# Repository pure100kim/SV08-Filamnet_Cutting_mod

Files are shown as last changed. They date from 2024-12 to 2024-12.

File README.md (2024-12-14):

# SV08 Filament Cutting MOD

Bamboo Hotend integrated filament cutting mode.

I have modified the STEP CAD file available on Sovol's GitHub.
Thank you to Sovol for providing the CAD STEP files.

https://github.com/Sovol3d/SV08/tree/main/STEP

<br>
<br>
<br>

**아래 동작 유투브 영상 참조하세요~** 
(Please refer to the YouTube video for the following steps~)

Refer to operation youtube video as below.

https://www.youtube.com/watch?v=FpVqoYQupSA

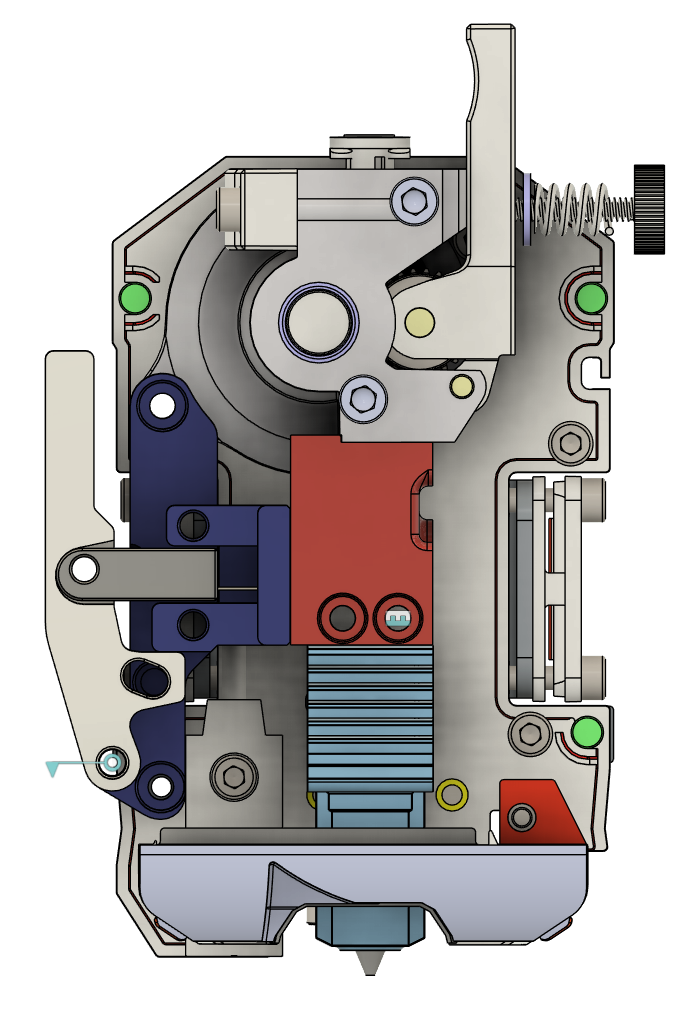
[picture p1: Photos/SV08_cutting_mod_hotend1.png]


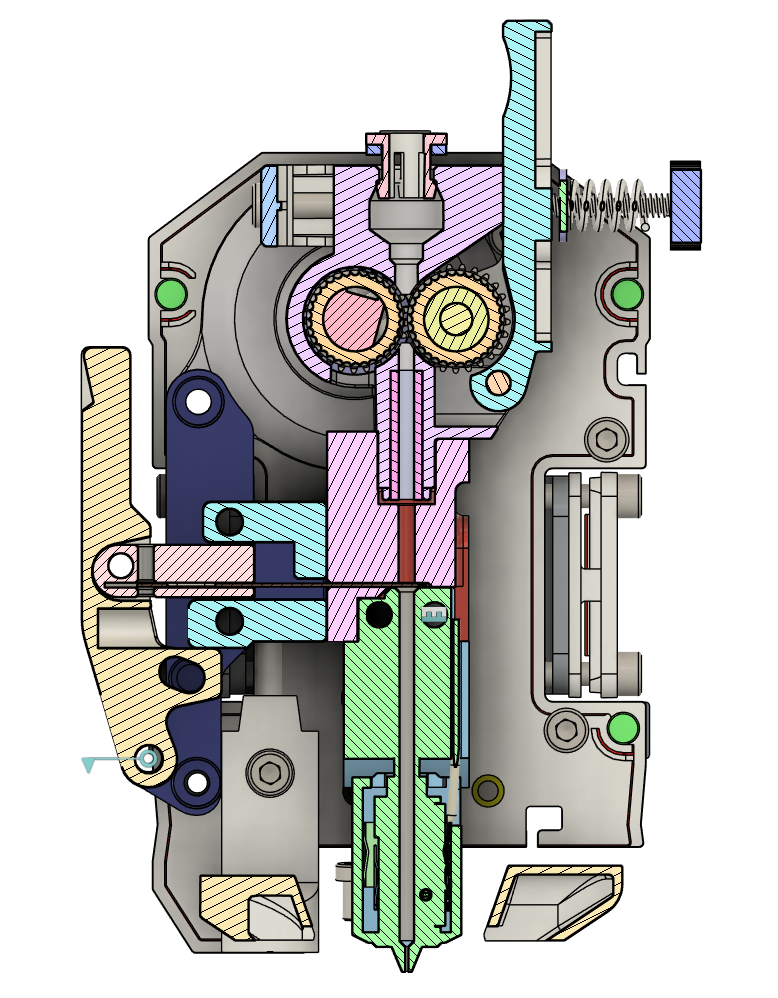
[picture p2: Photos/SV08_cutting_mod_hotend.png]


## **1. Prepare parts**

(1) Bambu HOTEND : 1ea

(2) Blade Cutter : 1ea

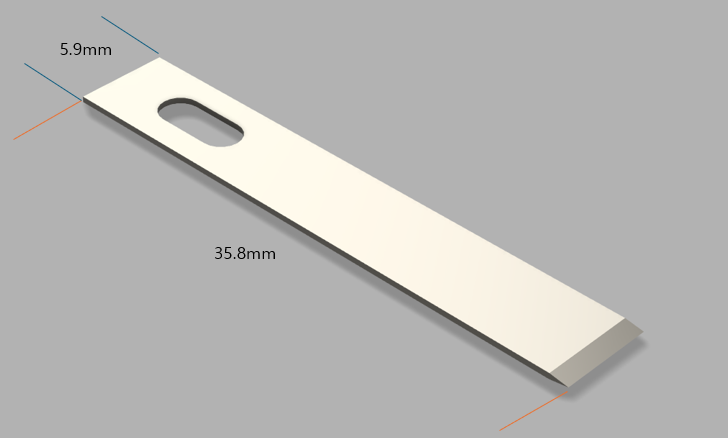
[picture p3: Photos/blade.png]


(3) M3 Insert : 5ea

(4) pen spring : 1ea

(5) space : 2ea

(6) M2*4mm : 1ea  (blade for fixing)

(7) M3*16mm : 3ea

(8) M3*20mm (SHCS) : 3ea

(9) M3*20mm (BHCS) : 2ea

(10) M3*8mm : 1ea

(11) M3 nut : 1ea (required loctite after joint)

(12) M4*20 : 1ea

<br>
<br>

## **2. Insert assembly**

인서트를 아래 사진과 같이 삽입을 합니다.<br>
The insert is inserted as shown in the image below.<br>

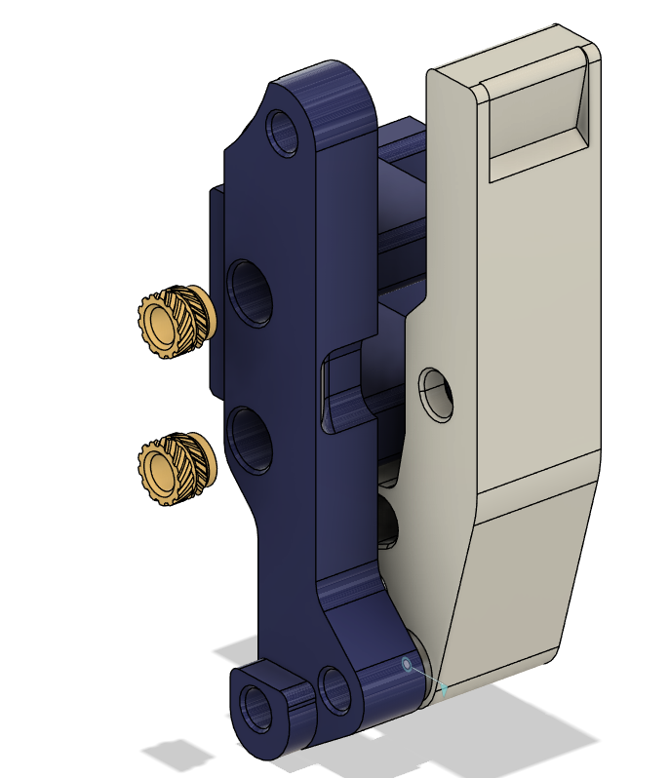
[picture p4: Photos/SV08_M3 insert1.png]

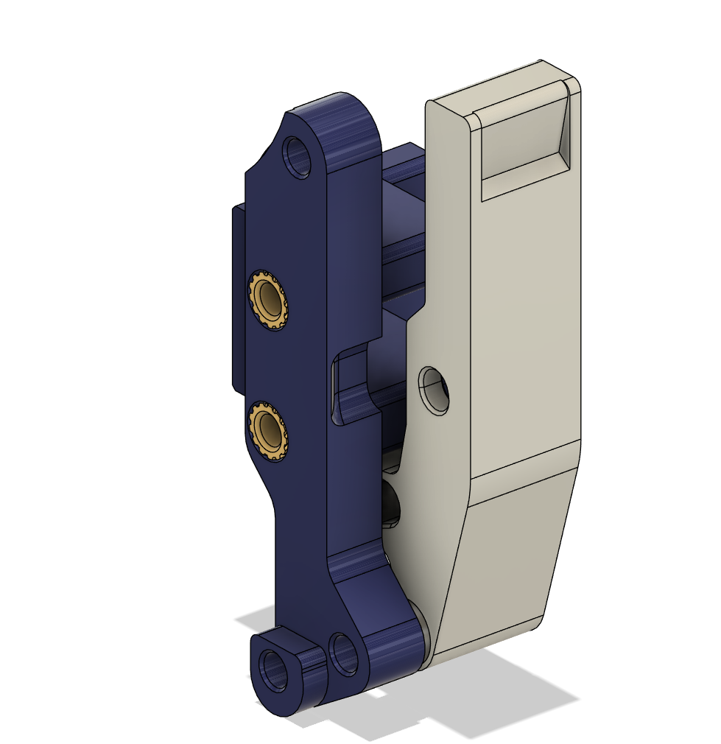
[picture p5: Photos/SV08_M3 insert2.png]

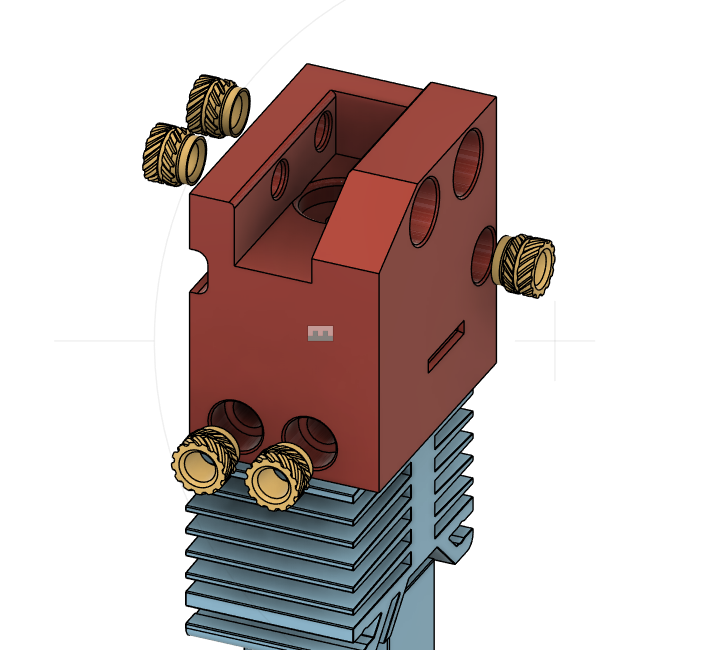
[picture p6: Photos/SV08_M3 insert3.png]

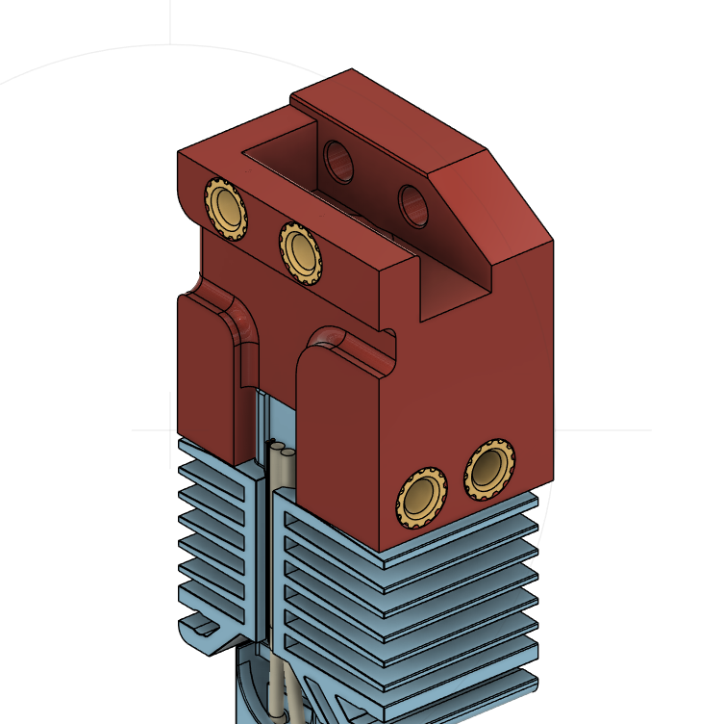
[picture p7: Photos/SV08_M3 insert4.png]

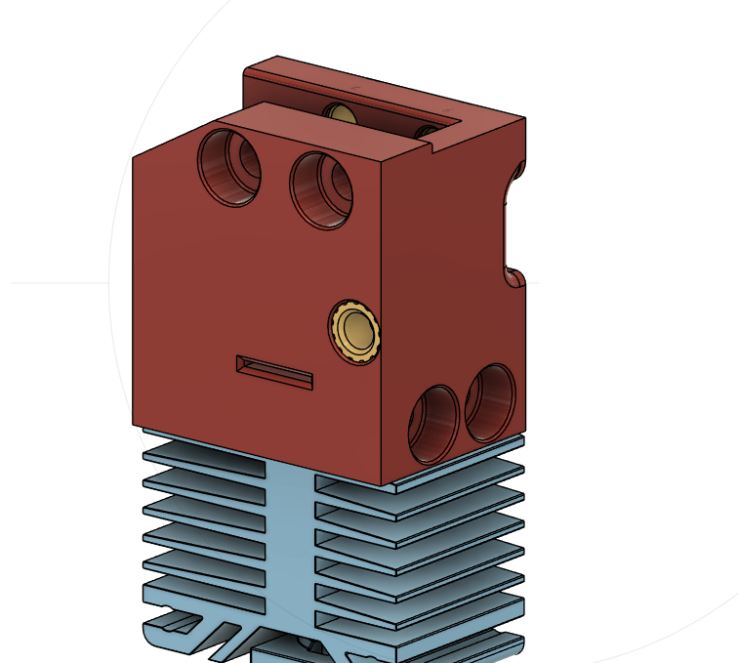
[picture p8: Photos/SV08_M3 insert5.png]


<br>

(1) HOTEND와 마운트를 먼저 체결합니다.<br>
First, attach the HOTEND and the mount. <br>
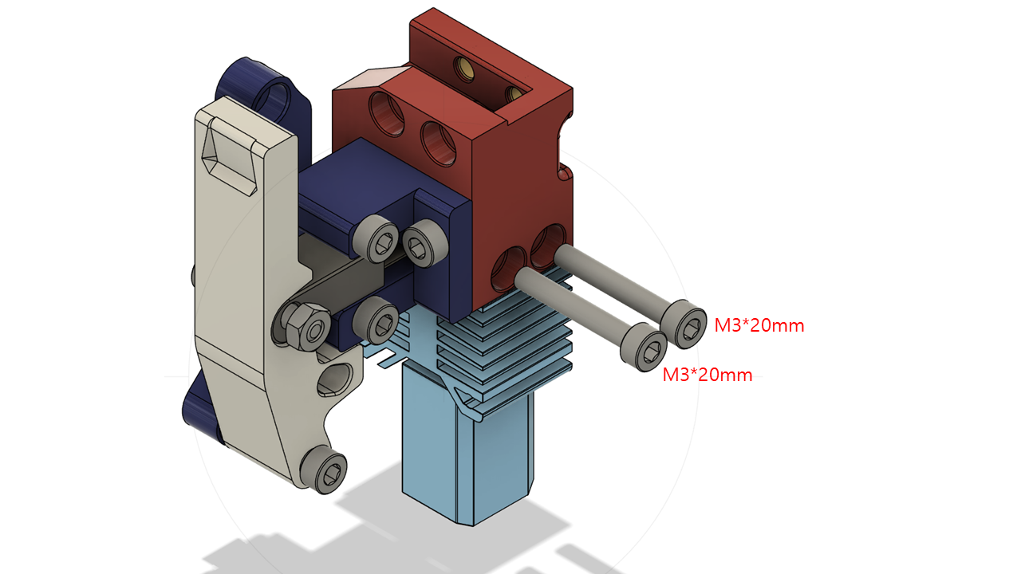
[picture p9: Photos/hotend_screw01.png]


<br>
<br>
(2) 마운트를 헤더에 체결을 합니다.<br>
Attach the mount to the header. <br>

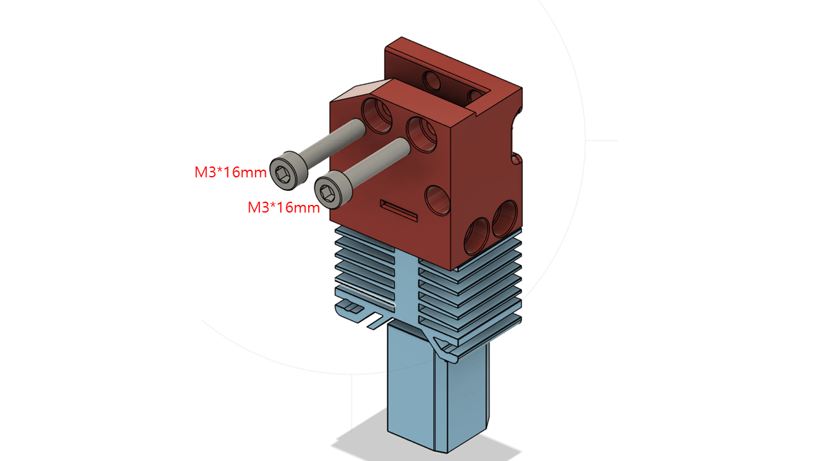
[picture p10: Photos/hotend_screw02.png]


<br>
<br>
(3) 레버 마운트를 헤더에 체결합니다.<br>
Attach the lever mount to the header. <br>

<br>
<br>
(4) 컷팅 가이드를 HOTEND 마운트와 체결합니다.<br>
Attach the cutting guide to the HOTEND mount. <br>

<br>
<br>
(5) 칼날과 칼날 마운트를 M2 볼트로 조립합니다.<br>
Assemble the blade and blade mount using M2 bolts. <br>

<br>
(6) 칼날 조립 부품을 헤더쪽에 가이드에 맞춰 삽입합니다.<br>
Insert the blade assembly component into the header, aligning it with the guide. <br>

<br>

(7) 칼날 가이드 레일을 레버 마운트와 M3*20mm 2개로 고정합니다.<br>
Secure the blade guide rail to the lever mount using two M3*20mm screws. <br>

(8) 레버 하단부 M3*20mm로 레버 마운트에 체결입니다.<br>
    M3 SPACE(와셔)를 양쪽에 넣어주면 좋습니다.<br>    
    (주의) 레버가 움직이도록 꽉 체결하지 말 것! 움직여야 합니다.<br>

Secure the lower part of the lever to the lever mount using an M3*20mm screw. <br>
It is recommended to insert M3 spacers (washers) on both sides. <br>
(Caution) Do not tighten the lever too firmly! It must remain movable. <br>

(9) 칼날 마운트 부품과 레버를 조립합니다. <br>
    M3 너트와 체결하며 록타이트로 너트가 빠지지 않도록 합니다.<br>
    (옵션) M3너트 안쪽에  M4 스페이스를 추가해도 됩니다.<br>    
    (주의) 칼날 마운트와 꽉 체결하지 말 것! 움직여야 합니다.<br>
Assemble the blade mount component with the lever. <br>
Secure them with an M3 nut, and apply Loctite to prevent the nut from loosening. <br>
(Optional) You may add an M4 spacer inside the M3 nut. <br>
(Caution) Do not tighten the blade mount too firmly! It must remain movable. <br>
    
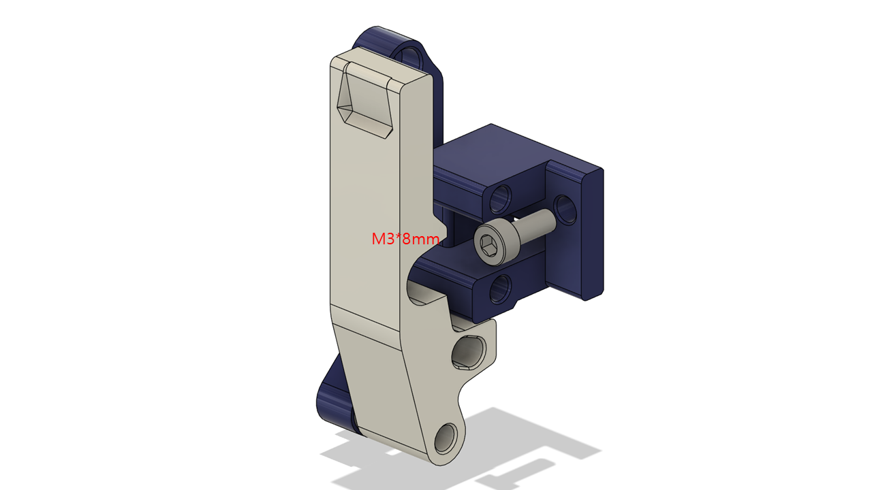
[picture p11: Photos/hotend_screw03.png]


(10) 레버를 움직이며 칼날이 자연스레 움직이는지 확인합니다. <br>
     (필수) 둥근머리 볼트(BHCS)를 사용해야 팬의 무두 볼트와 간섭이 생기질 않습니다.<br>
     (선택) 팬 고정 볼트를 둥근머리 볼트로 변경하여도 됩니다.<br>

 Move the lever to ensure the blade moves smoothly. <br>
(Mandatory) Use button head cap screws (BHCS) to avoid interference with the fan’s headless bolts. <br>
(Optional) You may also replace the fan mounting bolts with button head cap screws. <br>

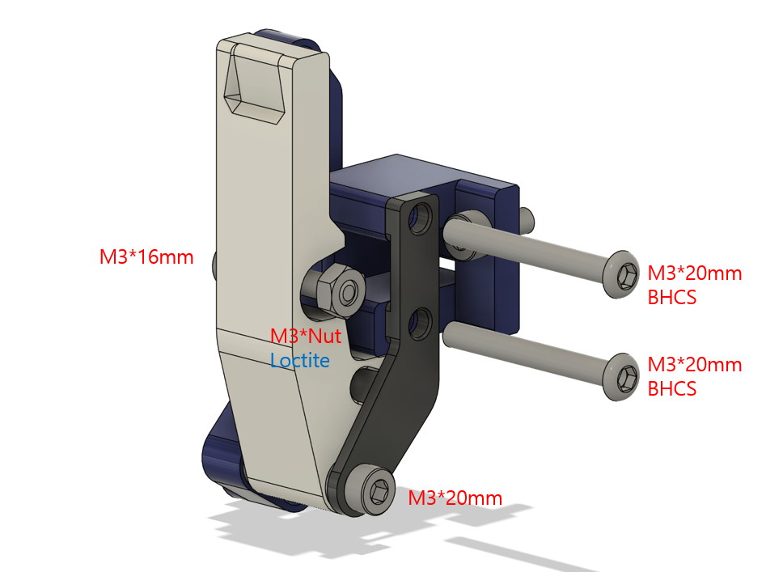
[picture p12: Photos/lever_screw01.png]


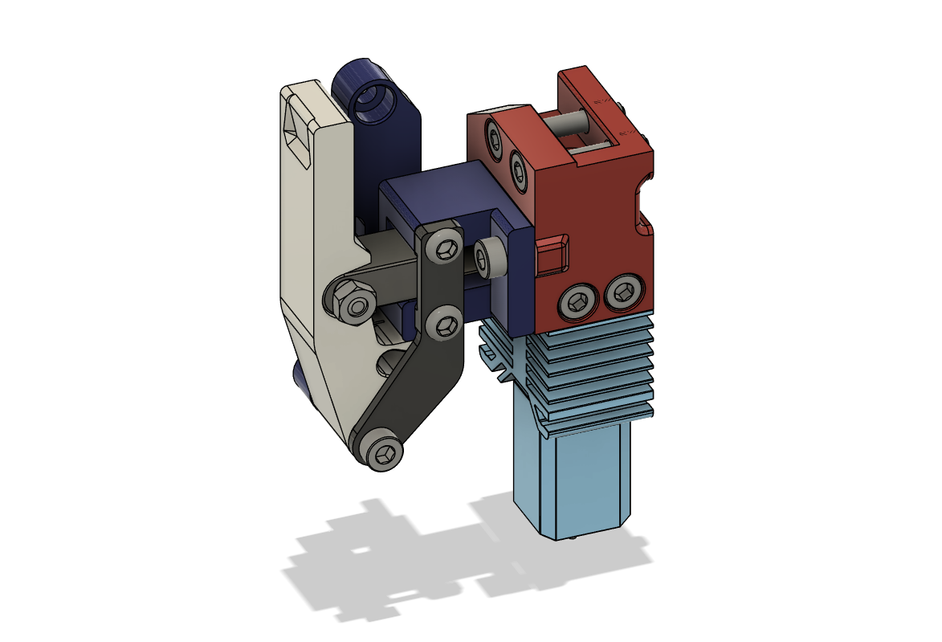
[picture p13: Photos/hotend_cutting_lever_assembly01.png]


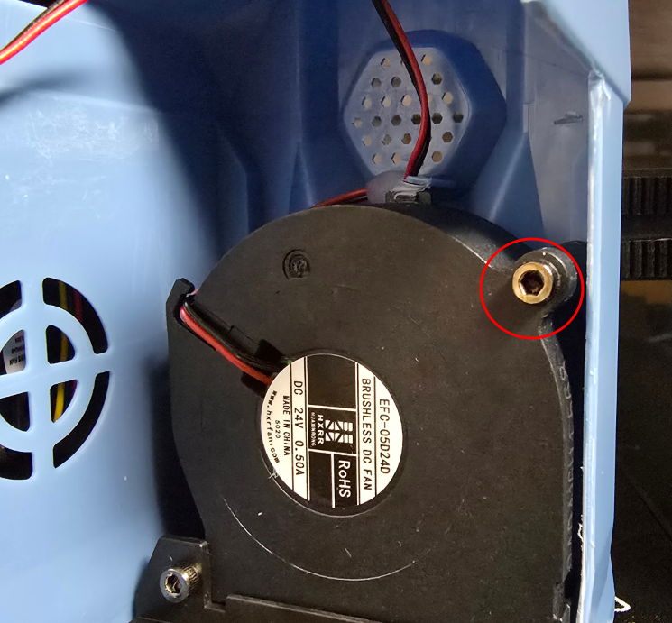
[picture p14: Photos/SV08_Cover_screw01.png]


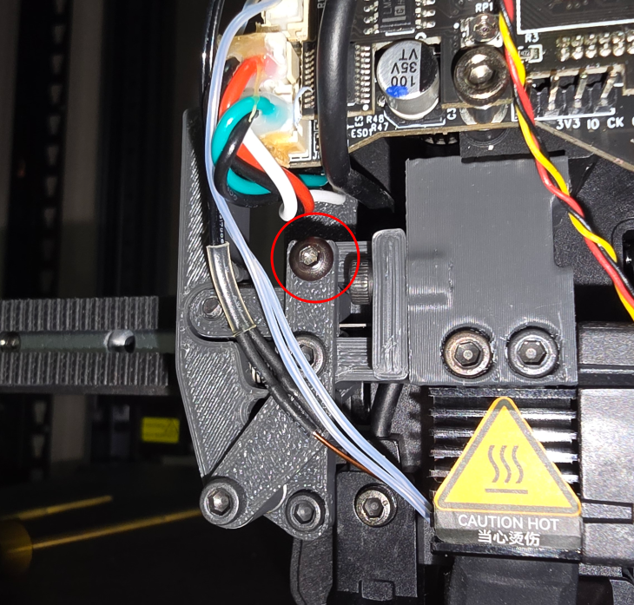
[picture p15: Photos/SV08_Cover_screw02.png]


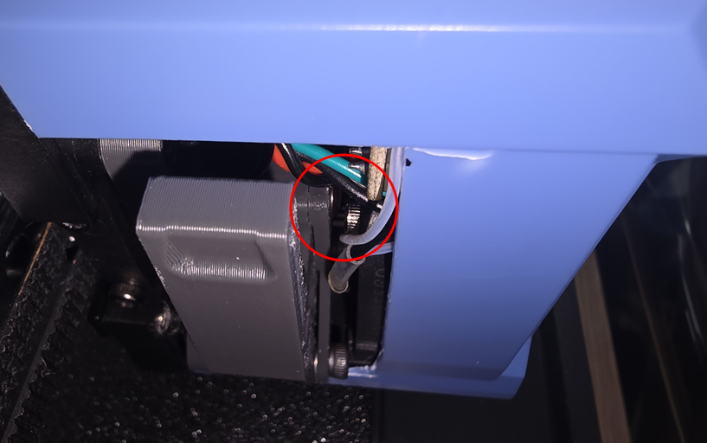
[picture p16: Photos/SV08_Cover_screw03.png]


<br>
<br>
<br>
(11) 레버 동작 고정 Push Bar를 설치합니다.<br>
Install the lever operation fixing push bar onto the X-axis belt mounting bracket.<br>

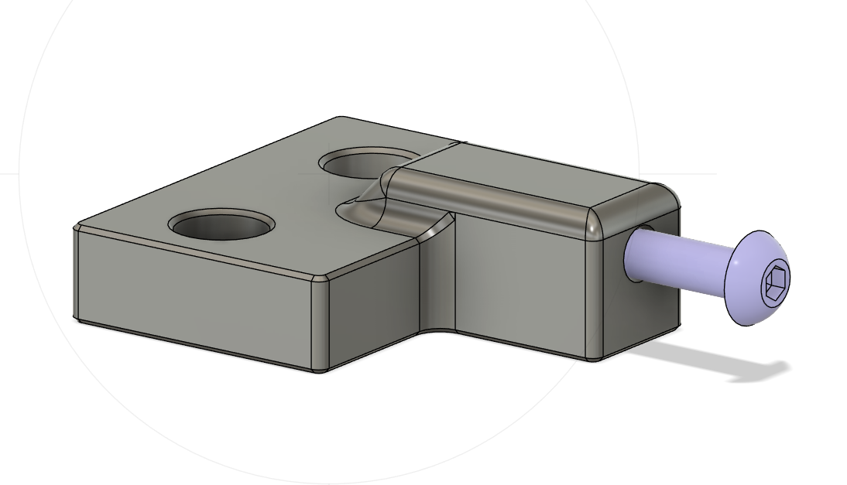
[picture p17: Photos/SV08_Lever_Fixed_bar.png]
.

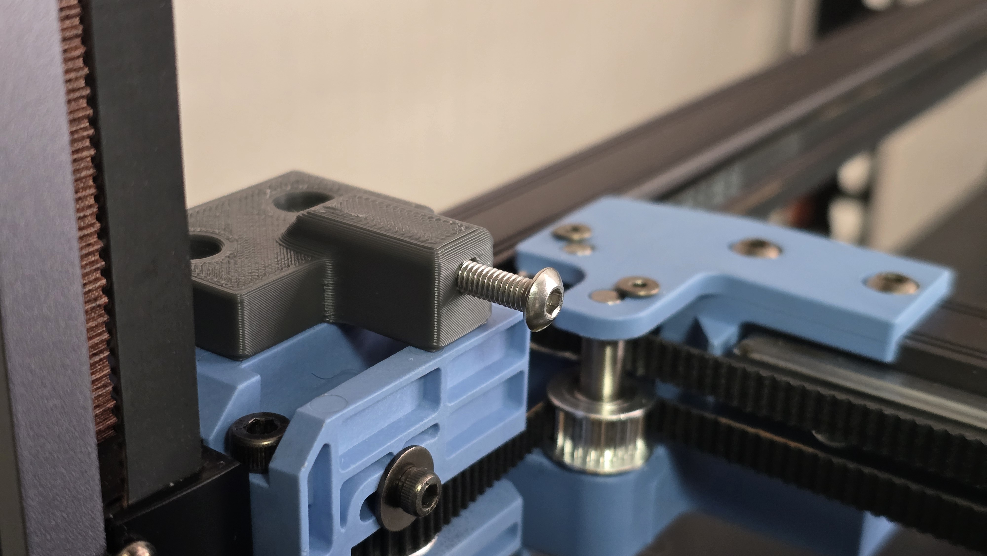
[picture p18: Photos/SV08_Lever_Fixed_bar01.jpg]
.

<br>
<br>
<br>

(12) 커버 레버 부분 절단(Cut out the cover lever section.)
<br>
블로워팬 경계 부분까지만 잘라냅니다.<br>
Cut only up to the boundary of the blower fan.<br>

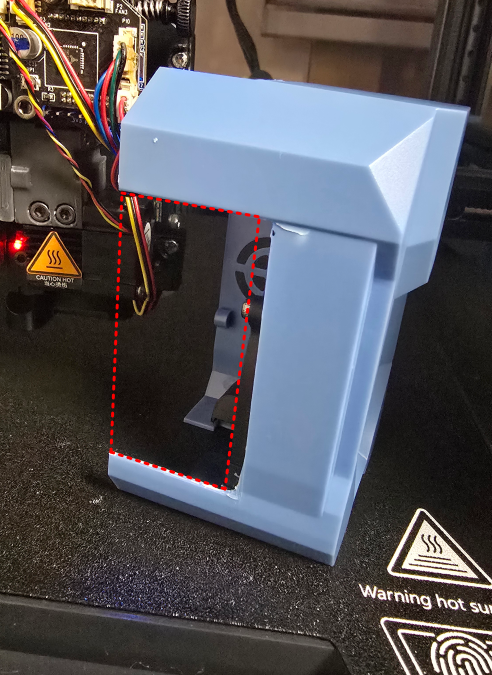
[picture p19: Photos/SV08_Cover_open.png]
.

<br>
<br>
<br>

## **5. ORCA Slice Machin start-G-code & macro.cfg Change **

(Mandatory) !!!!! Must chnage to all x positon over X10

필수로 꼭 수정하셔야 합니다.

[gcode_macro _global_var] <br>
variable_pause_park:{'x': 10, 'y': 0, 'z': 10, 'e': 1} <br>
variable_cancel_park:{'x': 10, 'y': 350, 'z': 10, 'e': 1} <br>

<br>
<br>
<br>

## **6. Add Chage Filament G-code** 

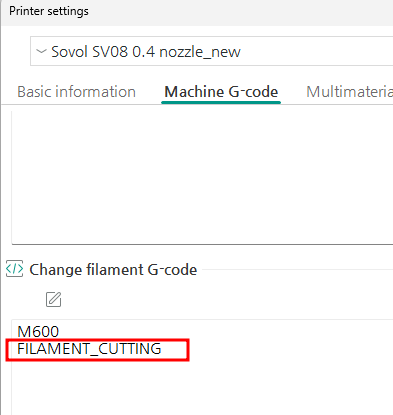
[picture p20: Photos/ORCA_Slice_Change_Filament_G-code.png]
.

<br>
<br>
<br>

## **7. Add macro G-code in Macro.cfg file** 

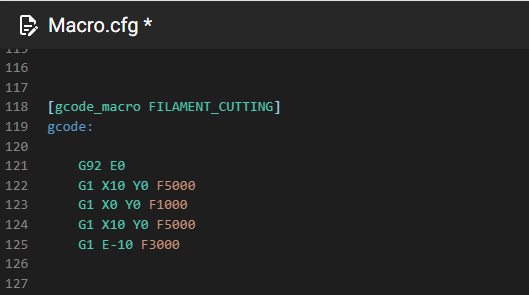
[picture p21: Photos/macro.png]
.

<br>
<br>
<br>

# SV08 Filament Cutting MOD Toolhead Hall Sensor Version (07.DEC 2024)

Toolhaed Hall Sensor version <bar>

(1) Micro swtich (D2F) : 1ea <br>

(2) 4mm Ball : 1ea <br>

(3) M3*20mm : 2ea <br>

(4) M2*10mm : 2ea <br>

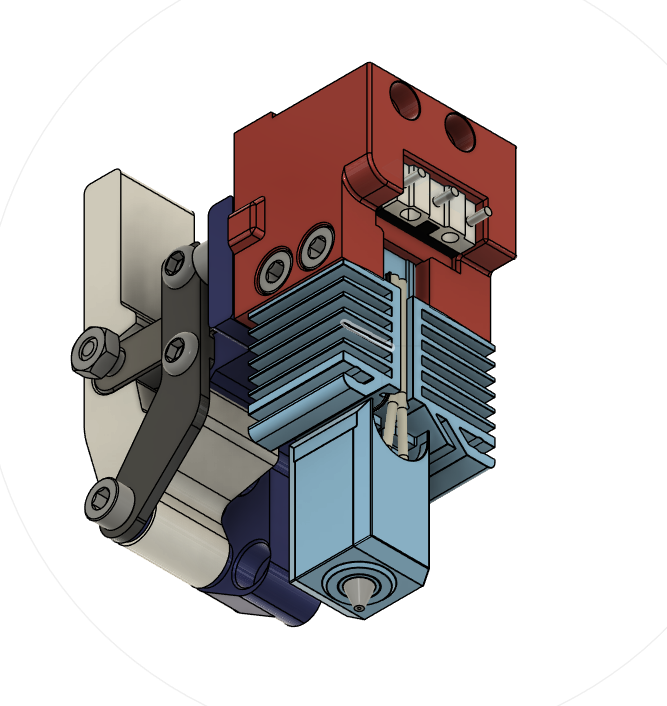
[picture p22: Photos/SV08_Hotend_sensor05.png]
.

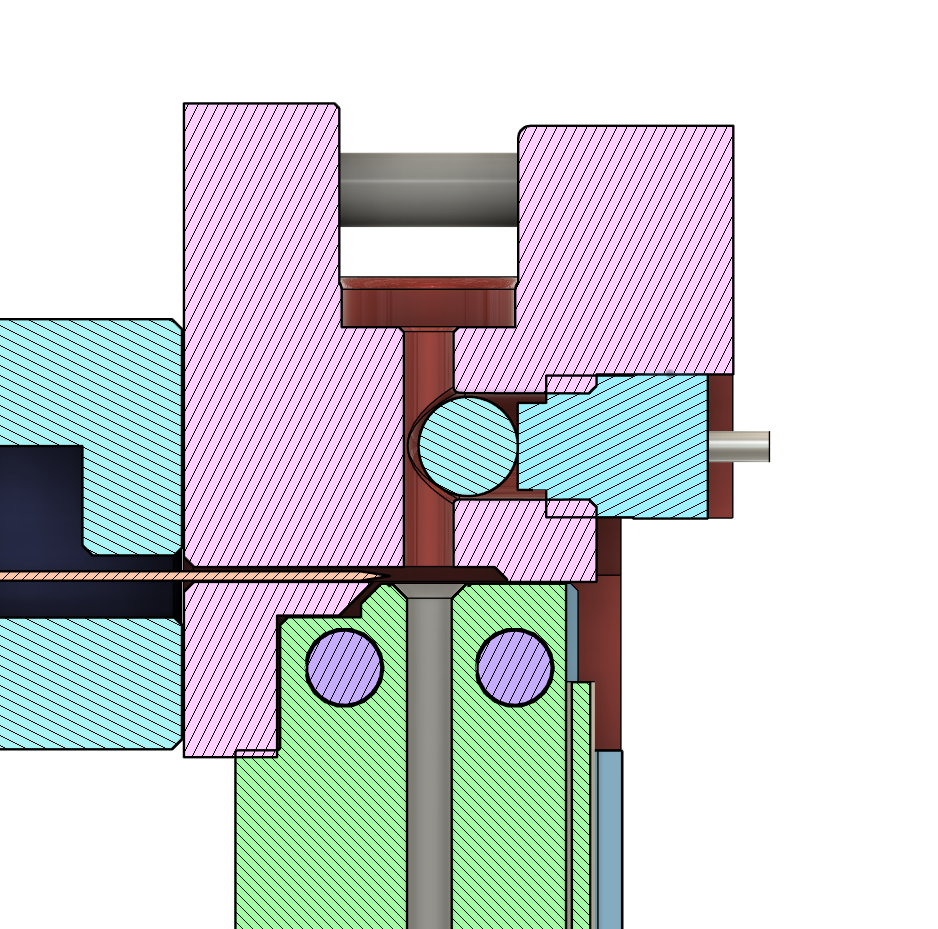
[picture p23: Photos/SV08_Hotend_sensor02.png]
.

## **8. Change note**

(1) Basic design NOV 20 ~ DEC.01 2024

(2) DEC 02 (Mon) : Modify lever M2*8mm screw interupt 

(3) DEC 02 (Mon) : screw assembly added

(4) DEC 04 (Wen) : Adjust torrence CAD, printout and assembly

(5) DEC 05 (Thu) : Add Lever & Guide holder.

(6) DEC 05 (Thu) : Push bar modeling

(7) DEC 05 (Thu) : Final Testing and macro coding

(8) DEC 06 (Fri) : Relased SV08 Filament Cutting mode

(9) DEC 07 (Sat) : Add Toolhead Hall sensor type HOTEND Mount

감사합니다.
Thank you!

미스터 굿맨 Mr.goodman

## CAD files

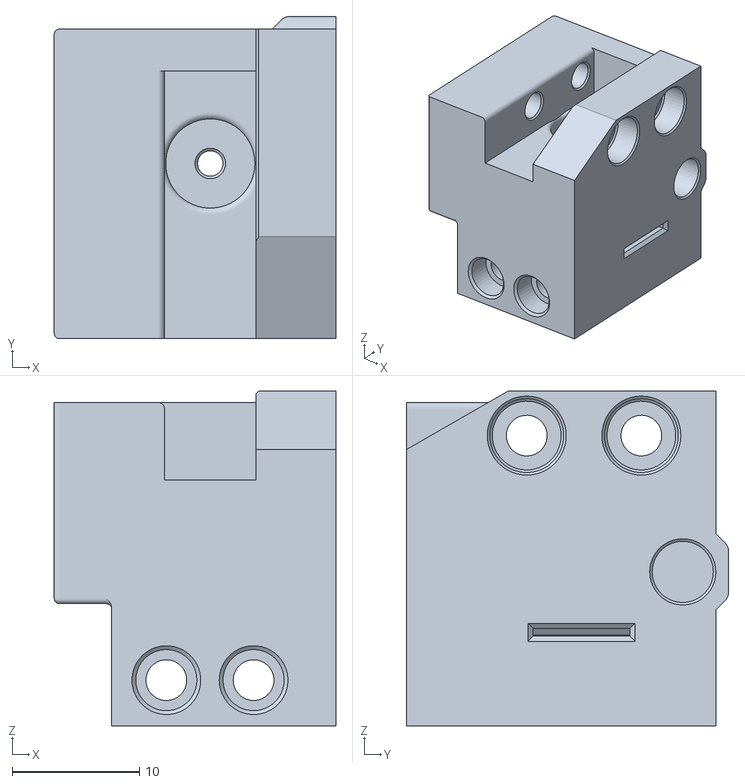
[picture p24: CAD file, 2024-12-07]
STL files/SV08_bambu_hotend_hall_sensor_mount.stl
22.1 x 25.3 x 26.3

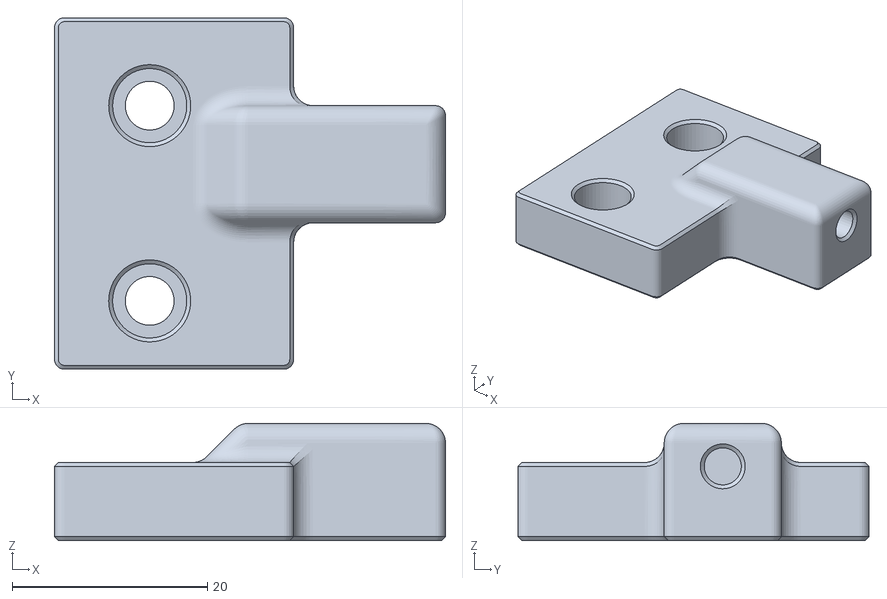
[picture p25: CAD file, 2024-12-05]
STL files/SV08_Lever_Fixed Bar.stl
40.1 x 36.0 x 12.0

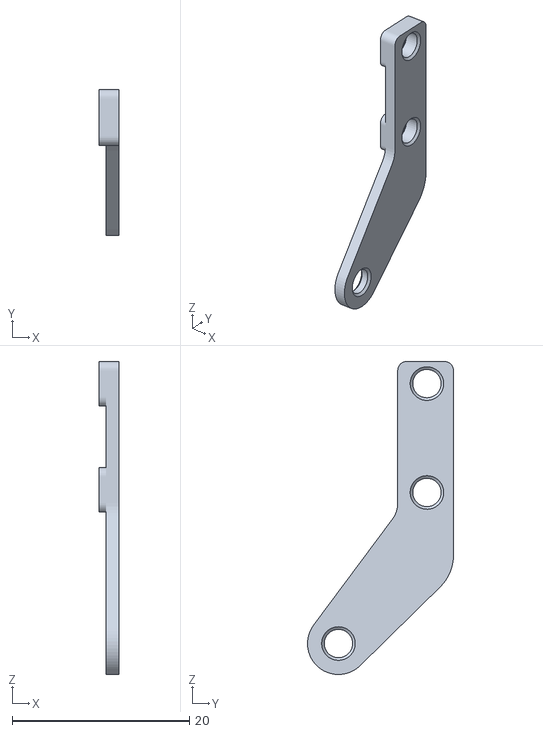
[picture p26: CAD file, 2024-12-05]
STL files/SV08_Lever_guide_holder.stl
2.30 x 16.5 x 35.4

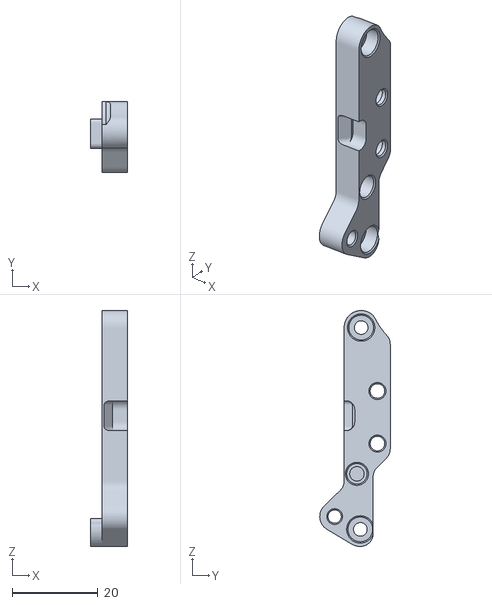
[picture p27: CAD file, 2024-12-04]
STL files/SV08_Cutting_lever_mount.stl
8.70 x 16.5 x 55.2

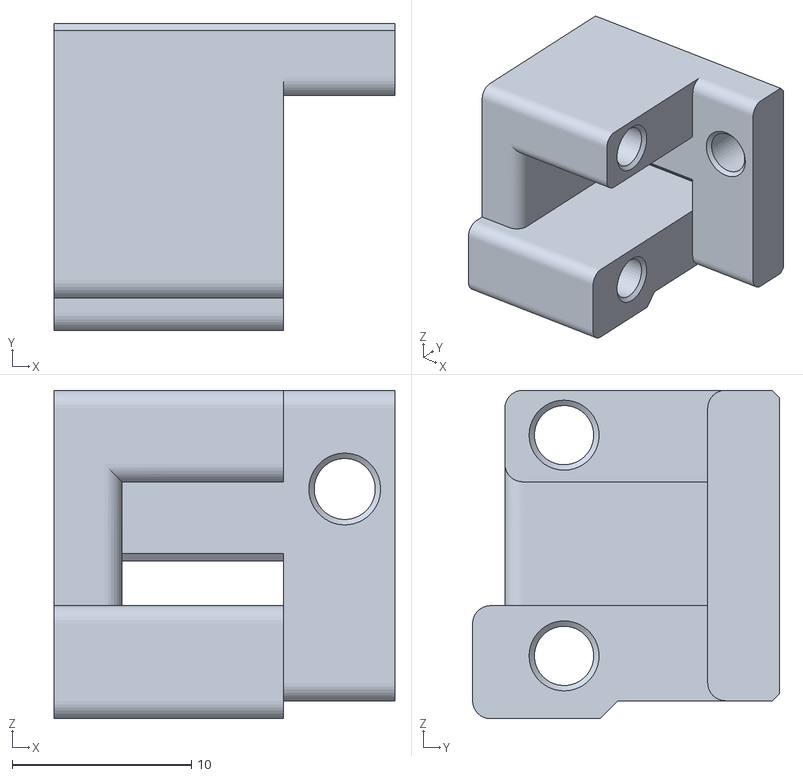
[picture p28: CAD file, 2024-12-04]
STL files/SV08_Hotend_Blade_holder_guide_mount.stl
19.0 x 17.1 x 18.3

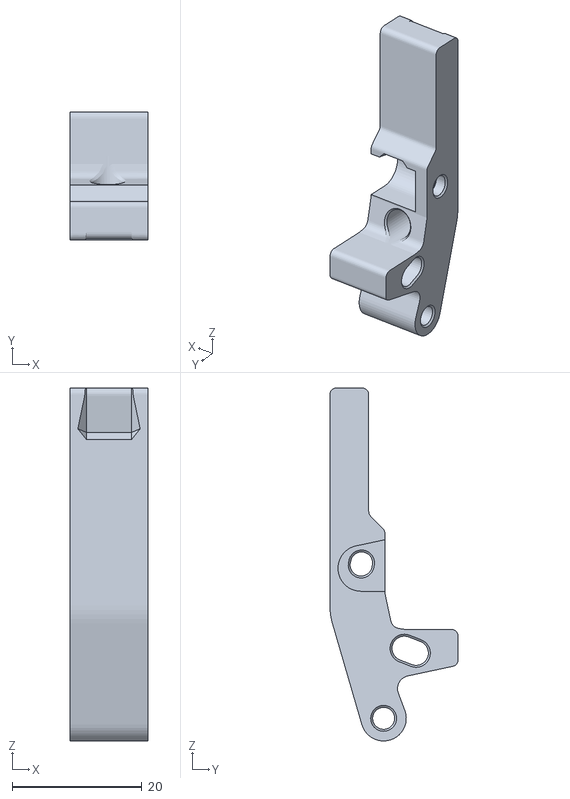
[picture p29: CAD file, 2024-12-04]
STL files/SV08_Cutting_Lever.stl
12.0 x 19.8 x 54.5

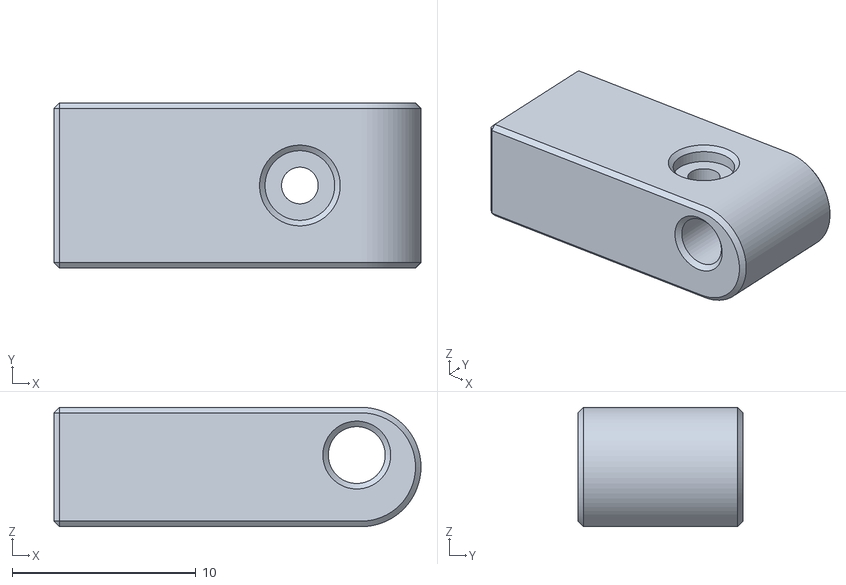
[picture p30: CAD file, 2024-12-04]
STL files/SV08_Blade_holder.stl
20.0 x 9.00 x 6.50

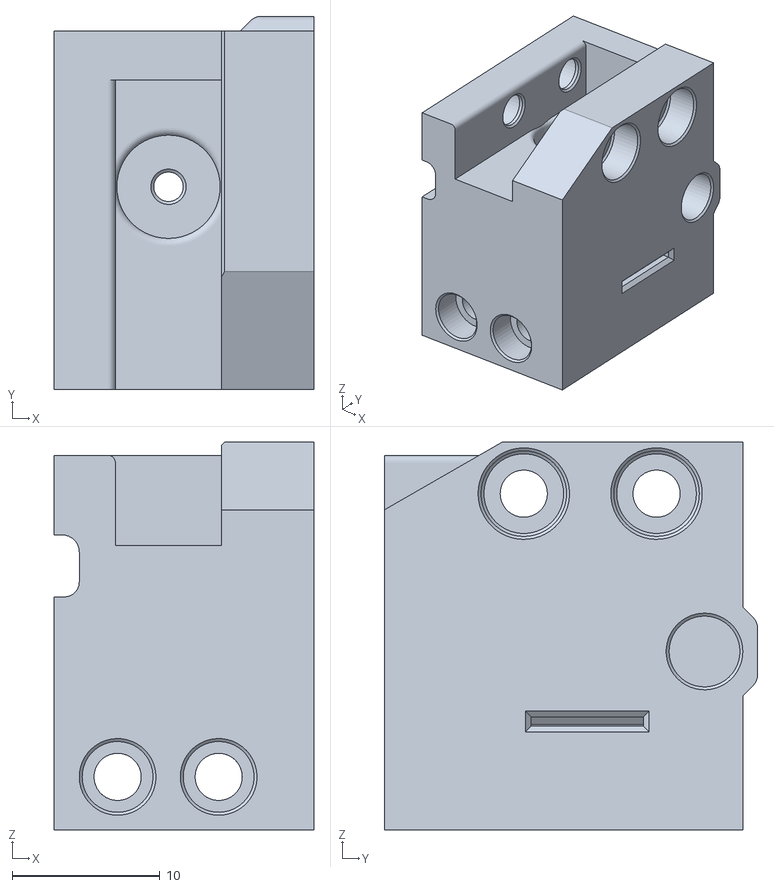
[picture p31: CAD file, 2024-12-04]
STL files/SV08_bambu_hotend_mount.stl
17.6 x 25.3 x 26.3

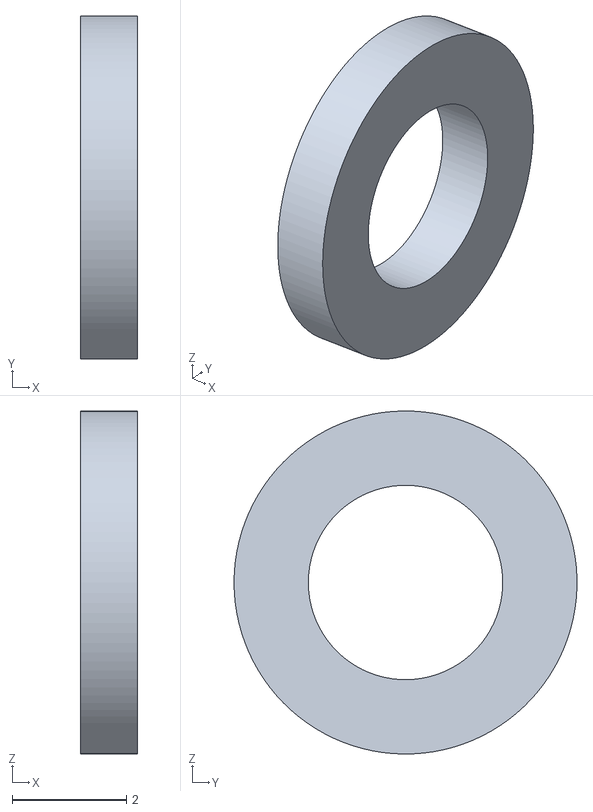
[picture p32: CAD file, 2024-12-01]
STL files/space_1mm.stl
1.00 x 6.00 x 6.00

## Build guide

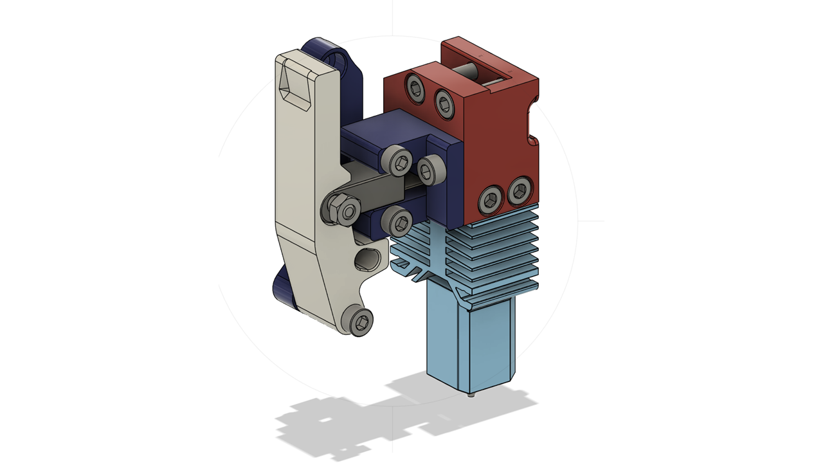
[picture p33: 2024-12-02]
Photos/hotend_cutting_lever_assembly.png
